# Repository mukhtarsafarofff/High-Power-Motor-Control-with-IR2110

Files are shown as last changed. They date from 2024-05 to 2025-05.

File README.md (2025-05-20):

(ENG) The IR2110 is a popular h-bridge half driver. It is designed to drive high voltage MOSFET and IGBT circuits. It does this without the use of p-channel MOSFETs or photovoltaic opto-couplers. The circuit generates HIGH side MOSFET gate voltage from a diode, bootstrap capacitor combination. The IR2110 is an 14-pin DIP IC and I used 2 for a complete h-bridge. The schematic to each half is identical. I used the 15V MOSFET/IGBT gate voltage with a 5-volt regular to supply the digital voltage (VDD) of 5V. The motor power supply is separate and is limited by the MOSFETs used and motor voltage up to 500-volts.  IR2110 illustration :
1) Pin 9 or VDD is the digital logic positive voltage range 3-15V. This enables the use of CMOS or LS TTL logic.
2) The VDD voltage depends on the type of logic connected to the inputs. I used a 5V Arduino so I connected 5V from a voltage regulator.
3) If using 3V logic such as Raspberry Pi GPIO connect to 3V. If using CMOS logic at say 12V connect VDD to 12V.
4) Pin 10 or HIN controls the output on pin 7 labeled HO that controls the HIGH side MOSFET. This input must be pulse-width-modulated as explained below.
5) Pin 12 or LIN controls the LOW side MOSFET connected to pin 1 LO. A HIGH outputs 10-15V on pin 1 turning on the LOW side MOSFET.
6) Pin 11 or SD will disable all outputs when HIGH. This is mostly connected to digital ground.
7) Pins 10, 11, and 12 all have Schmitt trigger inputs and internal pull down resistors.
8) Pin 13 or VSS is the digital power supply negative ground. This is often connected to motor supply HV voltage ground COM or pin 2.
9) Pins 8 and 14 no connection.

Now comes the tricky part the output. The IR2110 uses to "bootstrap" capacitor to supply the gate turn on voltage for MOSFET Q1. MOSFETs Q1 and Q2 are connected in a "totem pole" configuration. Pin 7 supplies the gate drive voltage for HIGH side MOSFET Q1. Pin 1 supplies the gate drive voltage for LOW MOSFET Q2. Notice the internal "totem pole" outputs from LO and HO within the IR2110. VCC pin 3 is 10-15V gate drive voltage. Each have internal under voltage (UV) detectors. When the gate voltage drops below ~8.5V outputs are turned off. Capacitor Cb is charged through a diode from VCC to 15V. Internal transistor "A" will switch the capacitor voltage to gate Q1. Cb can no longer charge from VCC until Q1 is turned off. It is the charge-discharge of Cb connected across Q1 that keeps Q1 turned on. RL represents the load (motor for example) and the LOW side MOSFET turned on at the other half of the h-bridge. Capacitor Cb in my circuit is a 0.22uF or 220n. It is charged to 15V through diode D1. In my case I used a 1N4007. For high speed switching a UF4007 high speed diode must be used. D1 also serves to block the motor drive voltage from 15V VCC. The capacitor charges to 15V across VB and VS when Q1 is off. VS is connected to Q1 source connection. When a HIGH is input to HIN the voltage at VB is switched to pin HO turning on Q1. Once Q1 is turned on the motor voltage appears at Q1 source preventing any further charging of Cb. Cb will discharge the rate related to MOSFET leakage, etc. Most internet sites connect a 1K resistor across Q1 gate-source, I removed it. They also connected a 22uF electrolytic across Cb I removed that. They also failed to bypass VCC so I added 22uF capacitor to ground. I removed a 22uF bypass capacitor across VDD as not needed. Diode D2 was a 1N4007 in the test circuit. I used a 1N4148 high speed diode in the final circuit. MOSFETs tested: IRFZ40 - VDS = 60V; ID = 36A and IRFZ44N - VDS = 55V; ID = 49A. The following from IR application note AN978-b. VDD is 3-15V, the output stage is implemented either with two N-Channel MOSFETs in totem pole configuration. Each IR2110 MOSFET can sink or source gate currents up to 2A, depending on the MGD. MGD stands for MOS-gate-driver. To quote in regards to VB, VS, and HO: The gate charge for the high side MOSFET is provided by the bootstrap capacitor which is charged by the 15V supply through the bootstrap diode during the time when the device is off. The use of pulses greatly reduces the power dissipation associated with the level translation. The pulse discriminator filters the set/reset pulses from fast dv/dt transients appearing on the VS node so that switching rates as high as 50V/ns in the power devices will not adversely affect the operation of the MGD. This channel has its own undervoltage lockout ( on some MGDs) which blocks the gate drive if the voltage between VB and VS, i.e., the voltage across the upper totem pole is below its limits (typically 8.7/8.3V). The operation of the UV lockout differs from the one on VCC in one detail: the first pulse after the UV lockout has released the channel changes the state of the output. The high voltage level translator circuit is designed to function properly even when the VS node swings below the COM pin by a voltage indicated in the data sheet, typically 5 V. The following in my view is nonsense. I used a single 15V supply for VCC and the motor supply voltage. 12V should also work. It worked just fine with my h-bridge. Gate voltage must be 10-15V higher than the drain voltage. Being a high side switch, such gate voltage would have to be higher than the rail voltage, which is frequently the highest voltage available in the system. Code is here :

#define INAHI 5 // pwm input A HI MOSFET
#define INBHI 6 // pwm input B HI MOSFET
#define INALO 7 // input A LO MOSFET 
#define INBLO 8 // input B LO MOSFET

#define POT 0

#define SW1 2
#define SW2 3

int val;

void setup() {
  pinMode(INAHI, OUTPUT);
  pinMode(INBHI, OUTPUT);
  pinMode(INALO, OUTPUT);
  pinMode(INBLO, OUTPUT);

  digitalWrite(INAHI, LOW);
  digitalWrite(INBHI, LOW);
  digitalWrite(INALO, LOW);
  digitalWrite(INBLO, LOW);

  pinMode(SW1, INPUT);
  pinMode(SW2, INPUT);

  pinMode(SW1, INPUT_PULLUP);
  pinMode(SW2, INPUT_PULLUP);
}

void loop() {

  analogWrite(INAHI, 0);
  analogWrite(INBHI, 0);
  
  // INAHI HIGH and INBLO HIGH
  // INALO LOW and INBHI LOW
  while (!digitalRead(SW1))   {
    digitalWrite(INALO, LOW);
    digitalWrite(INBHI, LOW);
    val = analogRead(POT)/ 4 ;
    analogWrite(INAHI, val);
    digitalWrite(INBLO, HIGH); 
  }

  // INAHI LOW and INBLO LOW
  // INALO HIGH and INBHI HIGH
  while (!digitalRead(SW2))   {
  digitalWrite(INAHI, LOW);
  digitalWrite(INBLO, LOW);
  val = analogRead(POT)/ 4;
  analogWrite(INBHI, val);
  digitalWrite(INALO, HIGH); 
  }

} // end loop

(DEU)  Der IR2110 ist ein beliebter Halbbrückentreiber. Er ist dafür ausgelegt, Hochspannungs-MOSFET- und IGBT-Schaltungen zu steuern. Dies geschieht ohne die Verwendung von P-Kanal-MOSFETs oder photovoltaischen Optokopplern. Die Schaltung erzeugt die Gate-Spannung für den HIGH-Side-MOSFET aus einer Kombination von Diode und Bootstrap-Kondensator. Der IR2110 ist ein 14-poliges DIP-IC, und ich habe zwei davon für eine vollständige H-Brücke verwendet. Der Schaltplan für jede Hälfte ist identisch. Ich habe die 15V MOSFET/IGBT-Gate-Spannung mit einem 5-Volt-Regler verwendet, um die digitale Spannung (VDD) von 5V zu liefern. Die Motorstromversorgung ist separat und wird durch die verwendeten MOSFETs und die Motorspannung bis zu 500 Volt begrenzt. Illustration des IR2110: 
1) Pin 9 oder VDD ist die positive Logikspannung im Bereich von 3-15V. Dies ermöglicht die Verwendung von CMOS- oder LS-TTL-Logik.
2) Die VDD-Spannung hängt von der Art der Logik ab, die mit den Eingängen verbunden ist. Ich habe einen 5V-Arduino verwendet, daher habe ich 5V von einem Spannungsregler angeschlossen. Wenn Sie 3V-Logik wie Raspberry Pi GPIO verwenden, schließen Sie VDD an 3V an.
3) Wenn Sie CMOS-Logik mit beispielsweise 12V verwenden, schließen Sie VDD an 12V an.
4) Pin 10 oder HIN steuert den Ausgang an Pin 7, bezeichnet als HO, der den HIGH-Side-MOSFET steuert. Dieser Eingang muss wie unten erläutert pulsweitenmoduliert werden.
5) Pin 12 oder LIN steuert den LOW-Side-MOSFET, der an Pin 1 LO angeschlossen ist. Ein HIGH gibt 10-15V an Pin 1 aus und schaltet den LOW-Side-MOSFET ein.
6) Pin 11 oder SD deaktiviert alle Ausgänge, wenn er auf HIGH gesetzt ist. Dieser ist meistens mit der digitalen Masse verbunden.
7) Pins 10, 11 und 12 haben alle Schmitt-Trigger-Eingänge und interne Pull-Down-Widerstände.
8) Pin 13 oder VSS ist die negative Masse der digitalen Stromversorgung. Diese ist oft mit der Masse der Motorversorgung (HV) verbunden, COM oder Pin 2.
9) Pins 8 und 14 sind nicht verbunden.
Nun kommt der knifflige Teil: der Ausgang. Der IR2110 verwendet einen "Bootstrap"-Kondensator, um die Einschaltspannung für das Gate des MOSFET Q1 bereitzustellen. Die MOSFETs Q1 und Q2 sind in einer "Totem-Pole"-Konfiguration verbunden. Pin 7 liefert die Gate-Ansteuerspannung für den HIGH-Side-MOSFET Q1. Pin 1 liefert die Gate-Ansteuerspannung für den LOW-Side-MOSFET Q2. Beachten Sie die internen "Totem-Pole"-Ausgänge von LO und HO innerhalb des IR2110. Der VCC-Pin 3 ist eine Gate-Ansteuerspannung von 10-15V. Jeder hat interne Unterspannung (UV)-Detektoren. Wenn die Gate-Spannung unter etwa 8,5V fällt, werden die Ausgänge abgeschaltet. Der Kondensator Cb wird über eine Diode von VCC auf 15V aufgeladen. Der interne Transistor "A" schaltet die Kondensatorspannung zum Gate von Q1. Cb kann sich nicht mehr von VCC aufladen, bis Q1 ausgeschaltet ist. Es ist das Lade-Entlade-Verhalten von Cb, der über Q1 verbunden ist, das Q1 eingeschaltet hält. RL stellt die Last dar (zum Beispiel einen Motor), und der LOW-Side-MOSFET ist in der anderen Hälfte der H-Brücke eingeschaltet. Der Kondensator Cb in meiner Schaltung ist 0,22 µF oder 220 nF. Er wird über die Diode D1 auf 15V aufgeladen. In meinem Fall habe ich eine 1N4007 verwendet. Für schnelles Schalten muss eine UF4007 Hochgeschwindigkeitsdiode verwendet werden. D1 dient auch dazu, die Motortreiberspannung von der 15V-VCC zu blockieren. Der Kondensator lädt sich auf 15V über VB und VS auf, wenn Q1 ausgeschaltet ist . VS ist mit dem Source-Anschluss von Q1 verbunden. Wenn ein HIGH-Signal an HIN angelegt wird, wird die Spannung an VB auf den Pin HO geschaltet und schaltet Q1 ein. Sobald Q1 eingeschaltet ist, erscheint die Motorspannung am Source-Anschluss von Q1 und verhindert eine weitere Aufladung von Cb. Cb entlädt sich mit einer Rate, die von der Leckstrom des MOSFETs und anderen Faktoren abhängt. Die meisten Internetseiten verbinden einen 1K-Widerstand zwischen Gate und Source von Q1, den habe ich entfernt. Sie haben auch einen 22uF-Elektrolytkondensator parallel zu Cb geschaltet, den habe ich ebenfalls entfernt. Sie haben VCC nicht gebypasst, also habe ich einen 22uF-Kondensator zur Erdung hinzugefügt. . Ich habe einen 22uF-Bypasskondensator parallel zu VDD entfernt, da er nicht benötigt wird. Diode D2 war im Testschaltkreis eine 1N4007. Ich habe in der endgültigen Schaltung eine 1N4148-Hochgeschwindigkeitsdiode verwendet. Getestete MOSFETs: IRFZ40 - VDS = 60V; ID = 36A und IRFZ44N - VDS = 55V; ID = 49A. Das Folgende stammt aus der IR-Anwendungsnote AN978-b. VDD beträgt 3-15V, die Ausgangsstufe wird entweder mit zwei N-Kanal-MOSFETs in Totem-Pole-Konfiguration implementiert. Jeder IR2110 MOSFET kann Gate-Ströme bis zu 2A aufnehmen oder abgeben, abhängig vom MGD. MGD steht für MOS-Gate-Treiber. Zitat zu VB, VS und HO: Die Gate-Ladung für den High-Side-MOSFET wird durch den Bootstrap-Kondensator bereitgestellt, der durch die 15V-Versorgung über die Bootstrap-Diode während der Zeit aufgeladen wird, in der das Gerät ausgeschaltet ist. Die Verwendung von Impulsen reduziert die Leistungsabgabe, die mit der Pegelübersetzung verbunden ist, erheblich. Der Impulsdiskriminator filtert die Set/Reset-Impulse von schnellen dv/dt-Übergängen, die am VS-Knoten auftreten, sodass Schaltgeschwindigkeiten von bis zu 50V/ns in den Leistungsbauteilen die Funktion des MGD nicht negativ beeinflussen. Dieser Kanal hat eine eigene Unterspannungssperre (bei einigen MGDs), die den Gate-Antrieb blockiert, wenn die Spannung zwischen VB und VS, d.h. die Spannung über dem oberen Totem-Pole, unterhalb ihrer Grenzwerte liegt (typischerweise 8,7/8,3V). Die Funktionsweise der UV-Sperre unterscheidet sich in einem Detail von derjenigen bei VCC: : Der erste Impuls nach dem Freigeben der UV-Sperre ändert den Zustand des Ausgangs. Die Hochspannungs-Pegelübersetzungsschaltung ist so ausgelegt, dass sie ordnungsgemäß funktioniert, selbst wenn der VS-Knoten unterhalb des COM-Pins um eine im Datenblatt angegebene Spannung, typischerweise 5V, schwingt. Das Folgende halte ich für Unsinn.  Ich habe eine einzige 15V-Versorgung für VCC und die Motorspannung verwendet.  12V sollte auch funktionieren. Es funktionierte einwandfrei mit meiner H-Brücke. Die Gate-Spannung muss 10-15V höher als die Drain-Spannung sein.  Als High-Side-Schalter muss eine solche Gate-Spannung höher als die Rail-Spannung sein, die häufig die höchste im System verfügbare Spannung ist.

#define INAHI 5
// pwm input A HI MOSFET
#define INBHI 6
// pwm input B HI MOSFET #define INALO 7
// input A LO MOSFET #define INBLO 8
// input B LO MOSFET

#define POT 0

#define SW1 2 #define SW2 3

int val;

void setup() { 
pinMode(INAHI, OUTPUT); 
pinMode(INBHI, OUTPUT);
pinMode(INALO, OUTPUT);
pinMode(INBLO, OUTPUT);

digitalWrite(INAHI, LOW); 
digitalWrite(INBHI, LOW); 
digitalWrite(INALO, LOW); 
digitalWrite(INBLO, LOW);

pinMode(SW1, INPUT); 
pinMode(SW2, INPUT);

pinMode(SW1, INPUT_PULLUP);
pinMode(SW2, INPUT_PULLUP); 
}

void loop() {

analogWrite(INAHI, 0);
analogWrite(INBHI, 0);

// INAHI HIGH and INBLO HIGH 
// INALO LOW and INBHI LOW 
while (!digitalRead(SW1)) {
digitalWrite(INALO, LOW);
digitalWrite(INBHI, LOW); 
val = analogRead(POT)/4;
analogWrite(INAHI, val); 
digitalWrite(INBLO, HIGH); }

// INAHI LOW and INBLO LOW 
//INALO HIGH and INBHI HIGH 
while (!digitalRead(SW2)) 
{ digitalWrite(INAHI, LOW); 
digitalWrite(INBLO, LOW); 
val = analogRead(POT)/ 4;
analogWrite(INBHI, val); 
digitalWrite(INALO, HIGH); }

} 
// end loop

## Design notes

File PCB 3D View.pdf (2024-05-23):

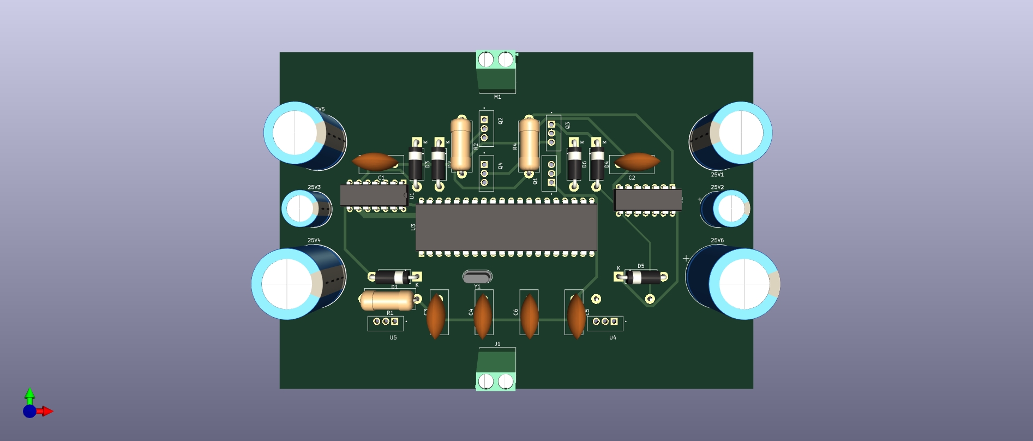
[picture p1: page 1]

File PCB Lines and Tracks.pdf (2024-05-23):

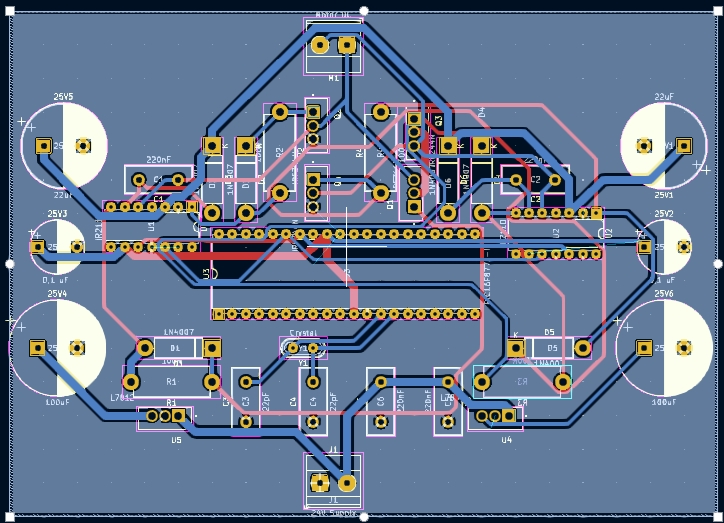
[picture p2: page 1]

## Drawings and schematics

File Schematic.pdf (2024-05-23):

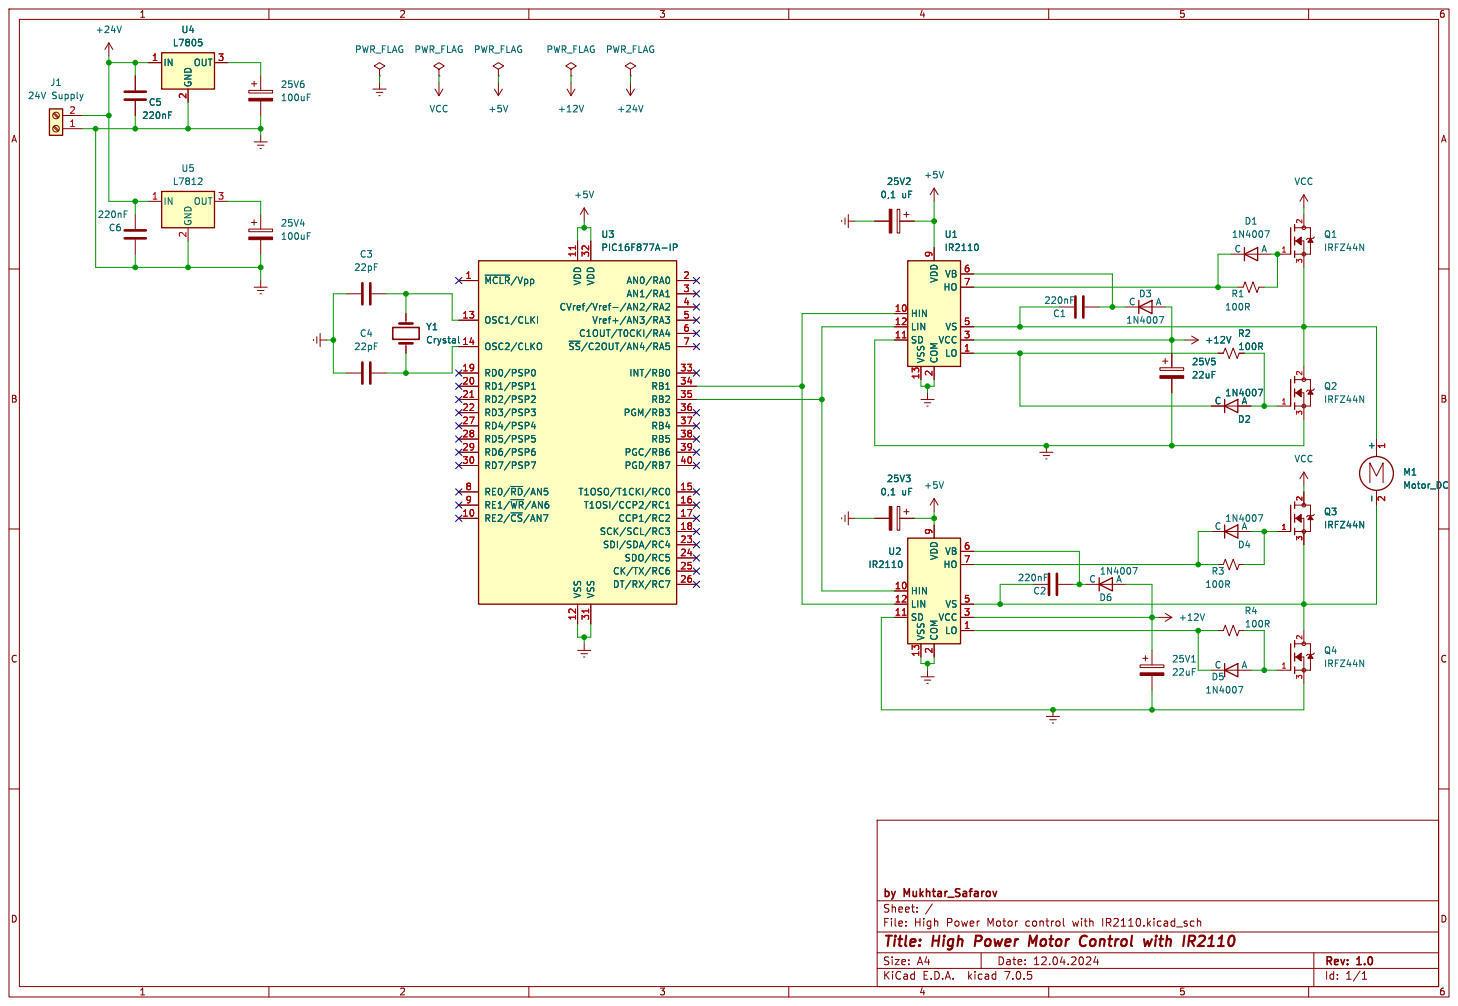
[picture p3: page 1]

2 VCC 3 VS 5 VB 6 HO VDD 7

Id: 1/1 Title: High Power Motor Control with IR2110

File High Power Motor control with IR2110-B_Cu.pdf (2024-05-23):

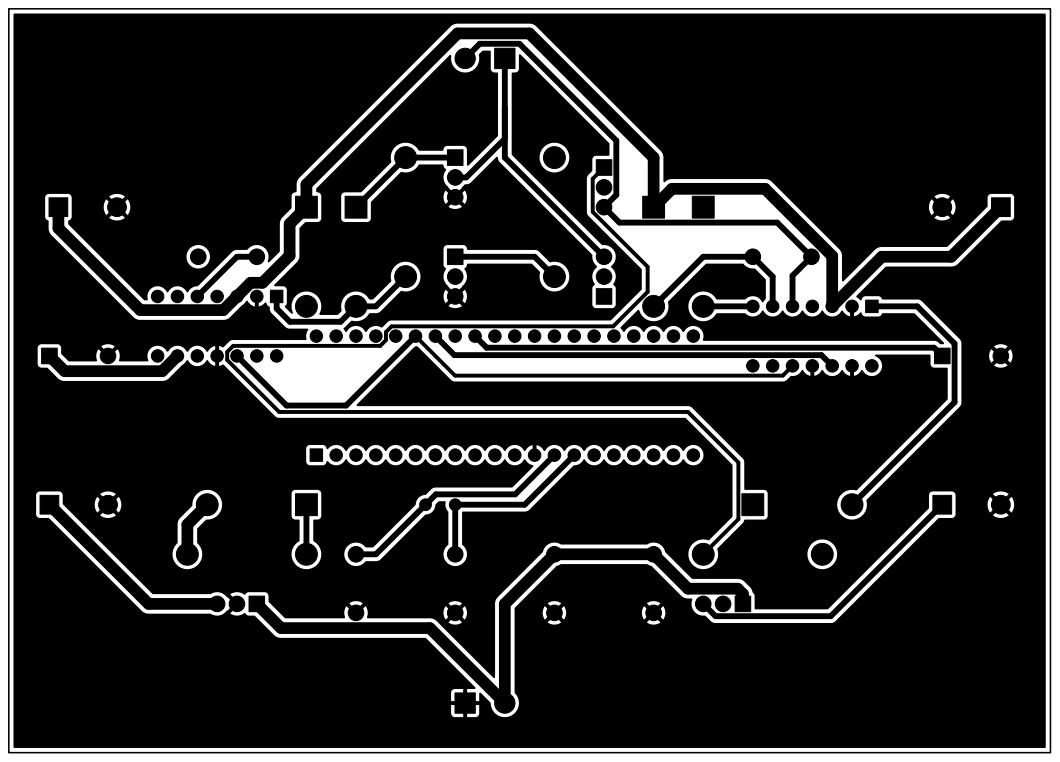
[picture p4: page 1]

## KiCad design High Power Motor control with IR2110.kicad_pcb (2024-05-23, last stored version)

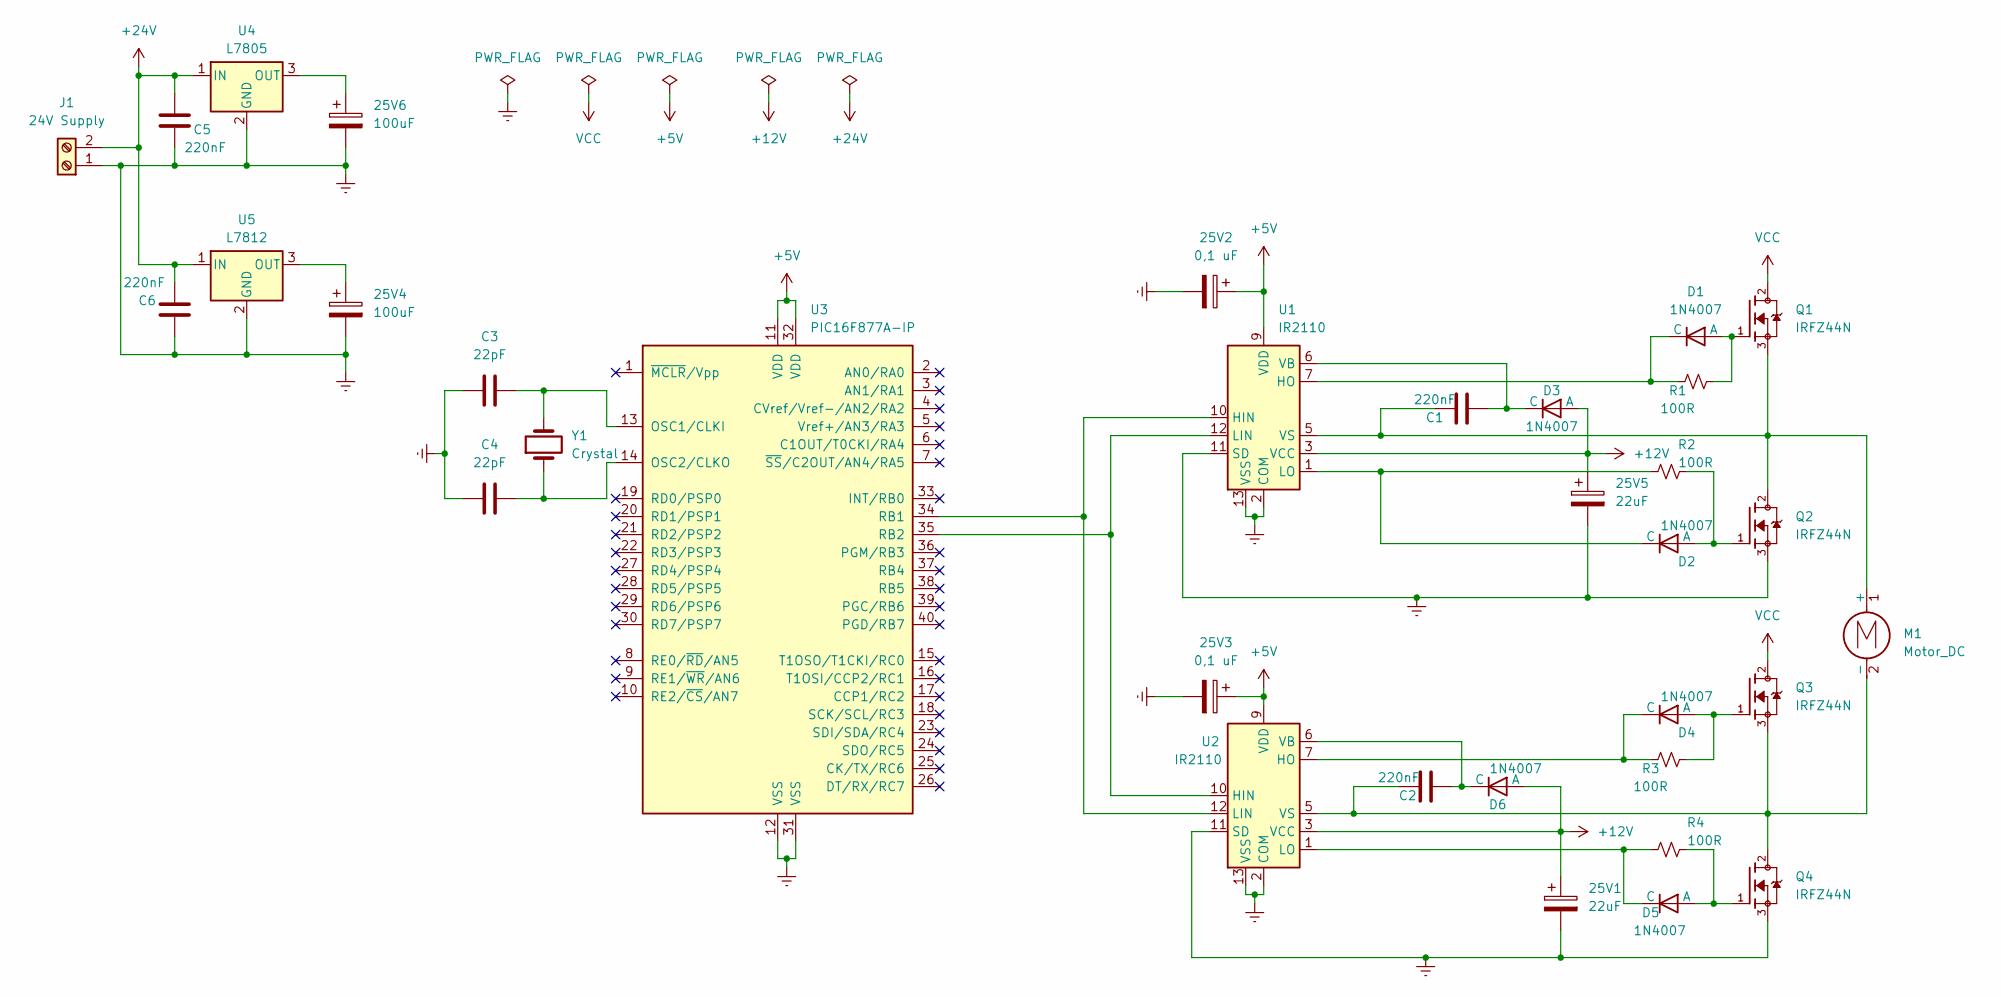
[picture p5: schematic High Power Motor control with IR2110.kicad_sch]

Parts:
25V1, 25V5: 22uF; CP_Radial_D16.0mm_P7.50mm
25V2, 25V3: 0,1 uF; CP_Radial_D10.0mm_P7.50mm
25V4, 25V6: 100uF; CP_Radial_D18.0mm_P7.50mm
C1, C2, C5, C6: 220nF; C_Disc_D12.5mm_W5.0mm_P7.50mm
C3, C4: 22pF; C_Disc_D12.5mm_W5.0mm_P7.50mm
D1, D2, D3, D4, D5, D6: 1N4007; D_5W_P12.70mm_Horizontal
J1: 24V Supply; TerminalBlock_Phoenix_MKDS-1,5-2-5.08_1x02_P5.08mm_Horizont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
M1: Motor_DC; TerminalBlock_Phoenix_MKDS-1,5-2-5.08_1x02_P5.08mm_Horizont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
Q1, Q2, Q3, Q4: IRFZ44N; TO254P1016X419X2286-3; PARTREV 09/21/10
R1, R2, R3, R4: 100R; R_Axial_DIN0614_L14.3mm_D5.7mm_P15.24mm_Horizontal
U1, U2: IR2110; DIP-14_W7.62mm
U3: PIC16F877A-IP; DIP-40_W15.24mm
U4: L7805; TO254P1016X419X2286-3
U5: L7812; TO254P1016X419X2286-3
Y1: Crystal; Crystal_HC52-6mm_Vertical

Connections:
+5V: 25V2.1, 25V3.1, U1.9 (VDD), U2.9 (VDD), U3.11 (VDD), U3.32 (VDD)
+12V: 25V1.1, 25V5.1, D3.1 (A), D6.1 (A), U1.3 (VCC), U2.3 (VCC)
Earth: 25V1.2, 25V2.2, 25V3.2, 25V4.2, 25V5.2, 25V6.2, C3.1, C4.1, C5.2, C6.1, J1.1, Q2.3, Q4.3, U1.2 (COM), U1.11 (SD), U1.13 (VSS), U2.2 (COM), U2.11 (SD), U2.13 (VSS), U3.12 (VSS), U3.31 (VSS), U4.2 (GND), U5.2 (GND)
unnamed: D1.1 (A), Q1.1, R1.1
unnamed: D1.2 (C), R1.2, U1.7 (HO)
unnamed: D2.1 (A), Q2.1, R2.1
unnamed: D2.2 (C), R2.2, U1.1 (LO)
unnamed: C1.2, D3.2 (C), U1.6 (VB)
unnamed: D4.1 (A), Q3.1, R3.1
unnamed: D4.2 (C), R3.2, U2.7 (HO)
unnamed: D5.1 (A), Q4.1, R4.1
unnamed: D5.2 (C), R4.2, U2.1 (LO)
unnamed: C2.2, D6.2 (C), U2.6 (VB)
unnamed: C5.1, C6.2, J1.2, U4.1 (IN), U5.1 (IN)
unnamed: C1.1, M1.1 (+), Q1.3, Q2.2, U1.5 (VS)
unnamed: C2.1, M1.2 (-), Q3.3, Q4.2, U2.5 (VS)
unnamed: U1.10 (HIN), U2.12 (LIN), U3.34 (RB1)
unnamed: U1.12 (LIN), U2.10 (HIN), U3.35 (RB2)
unnamed: C3.2, U3.13 (OSC1/CLKI), Y1.2
unnamed: C4.2, U3.14 (OSC2/CLKO), Y1.1
unnamed: 25V6.1, U4.3 (OUT)
unnamed: 25V4.1, U5.3 (OUT)
VCC: Q1.2, Q3.2

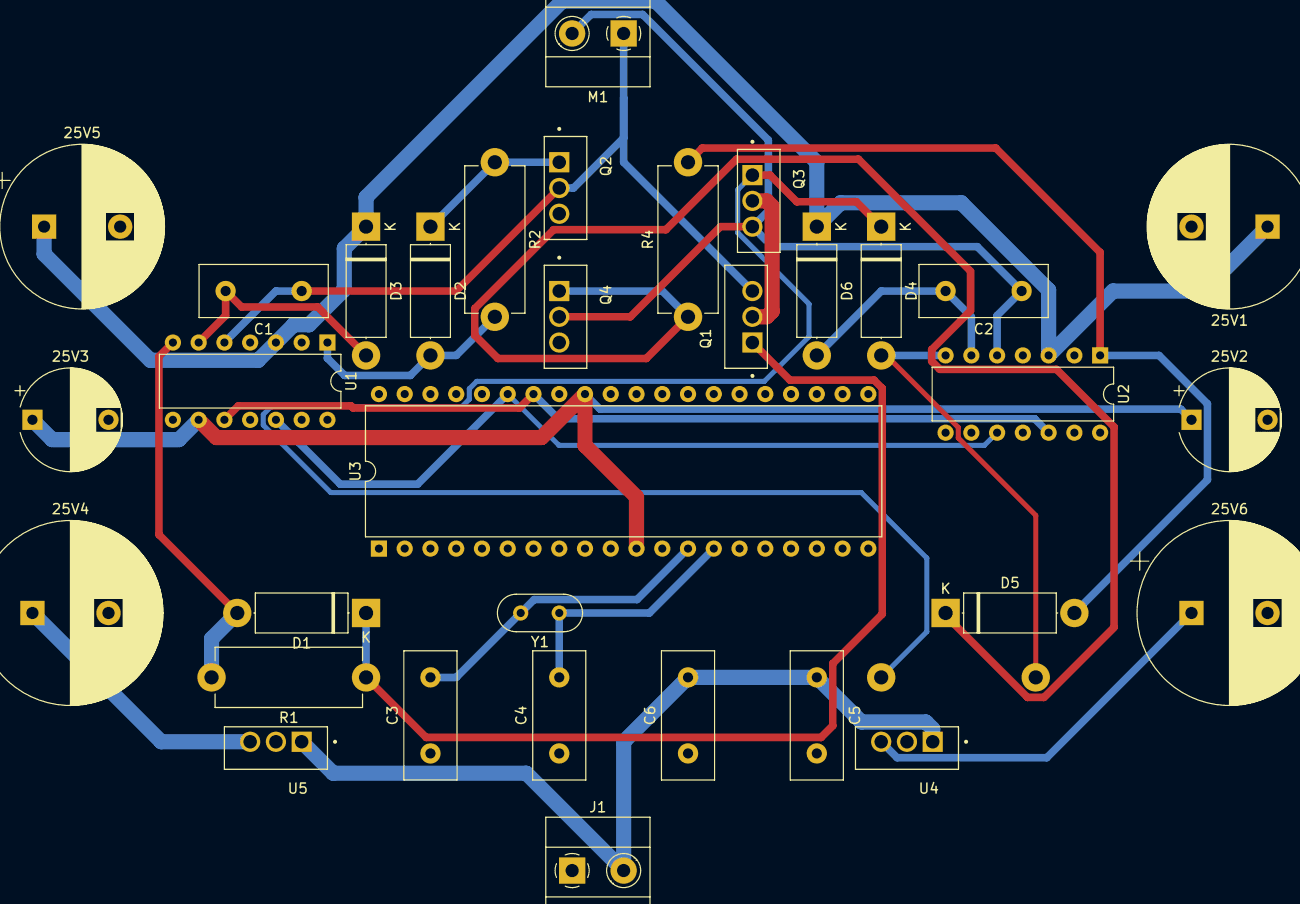
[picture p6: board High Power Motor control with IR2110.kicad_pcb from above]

Board: 2 copper layers, 34 parts (1 on the bottom side), 23 nets.
